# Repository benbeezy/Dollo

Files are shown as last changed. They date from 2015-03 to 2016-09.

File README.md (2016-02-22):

# Dollo
a fully printed 3D printer, that scales.

# Goals in order of priority

1) Make a 3D printer that can make as many of its own parts as possible

2) Have it so the machine can scale with little to no throwing away of old parts

3) Make it easy to assemble

4) Use no more than a single 1KG spool of plastic to make.

5) Make it as low cost as possible.

6) use parts that are easy to find.

7) make it durable (since it can print its own parts this isn't super high priority)

8) hope people stop asking "what if you could 3D print a 3D printer" because of course you can and its not that unique of an idea

# Part count and list for small Dollo

(x=number of slots times 2) -- rack_x_units.stl

13 -- extention.stl

8 -- corner.stl

156 -- bow_tie.stl but extra never hurts

96 —- long_ties.stl

2 -- x_spacer.stl

6 -- motor_mount.stl

8 -- twist_corner.stl

4 -- large_gear.stl

3 -- gear.stl

4 -- middle_gear.stl

1 -- gear_one.stl

1 -- hot_end_mount.stl

Metal parts we hope to get rid of in the future

11 -- M3x40  for the motor mounts and bed gears

5 -- M3x10  for the motor mounts and bed gears

4 -- M3x20  for the z motor

4 -- M3 lock nuts  for the bed gears

Electronics and other

1 - main controller board (we use RAMBo and also like the idea of printing the pcb and solding the components your self)

3 - end stop switches   we are trying to come up with a clever way of doing with with printed conductive parts

5 - motors

1 - hotend or whatever tool tip you want really

1 - hobbed thing, gear or bolt

1 - bearing for extruder (might be able to print)

1 - heated bed

1 - glass/aluminum that fits on the bed

4 - springs and screw for leveling your bed.

Options for a larger printer

8 - extention_3_units.stl  This will make it so your printer can fit a normal heated bed in the normal way and not limit the space at all

4 - extention_x_units & more twist_corner.stl. You can add as many of whatever size you want pieces into the z axis, this print doesn't been anything extra for those to work

# How to assemble
1) start with the basic frame, take a single corner and butt joint all 3 extension pieces to it with all 4 bow_tie slots. then on the end of each of those add corner pieces then extension pieces again until you have built out a full cube shape.

2) put on the racks. first you need to decide what side you want to be up, this really doesn't matter since it should be the same on all sides. Once you have figured that out, you can start putting your slots on the top of your printer with more bow ties add racks on parallel sides and to the top of your remaining extension piece. each should have 3 racks on it.

3) mounting your motors. first you will need to put a gear.scad on your motor shaft, then you can take a motor and put the motor_mount_small on it and screw in the single counter sunk screw on the bottom using a M3x10 and then put it on your printer rack and make sure the gear aligned with the rack teeth. once it does you can keep it on the rack and screw in your other motor_mount_small to the other side. (make sure to do this on the printer because if you don't it wont go on after) do this for all 3 racks and make sure the motor faces out.

4) mounting the x axis. grab your x_spacer and put them on the end of what you already have assembled on the left over extention piece and then slide that into the motor mount on each side of the printer.

5) Get the frame ready for the bed. first you need to prep you printer by taking the crazy looking twist_corner pieces and bow tie them to the inside of the printers frame mirroring each other but keep the bottom one out on each side.

6) now take a motor and mount put the gear_one on it and mount that to your bed, then take your middle_gear and put those next to the motor and then put your large_gear and large_twist together, and put those next in line. 

7) putting the bed in. This can be kind of tricky, but you have to twist your bed so it goes inside the frame sideways and the you should be-able to twist it to make it fit in the frame with the corners sticking out. and this is why we didn't put in the bottom corner_twists, because now your bed sits just under them and once you have the electronics set up it will be able to twist into those and once its in the teeth you will be able to add your last parts under it.

8) Electricity is fun. take all of your motor and put them into the correct stepper controllers making sure that your Y motors are plugged in opposite of each other. Plug in your electronics and make sure to upload the correct Dollo version of marlin. Once you have done this you should be able to move your motors and this is where you move your z motor in the negative direction (negative because that make the hotend and the bed closer) and once it is up at the top, you can put your last twist_corners on your printer.

9) hot ends and end stops. at the point of making this commit I do not yet have the end stops figured out. But the hotend should put in your hotend mount and should just slide and clip into your x motor mount. 

10) setting up the extruder. Not sure what extruder we are going to use yet, but if you have done 3D printing before you should know how all of that works and be able to get it going.

Z options) I do have the z axis all modeled for being fully printed and able to scale

# Extra cool facts

1) I came up with the original version of this when I was 16 and in high school and it was done in blender because thats all I knew how to use

2) This printer as it stands is under 1KG of printed parts 

3) We printed the first Dollo on 3 Prusa Mendal printer that were printer on other printers them selves and so on, all the way back to the start, so these machine have only open-source in their genealogy

4) I lived 300 miles from the printer that I used and did all of the printing over the internet using octopi to print the first Dollo

5) The Dollo can (if you want) have a metal core structure, we built it in just in case and it saved plastic so it was a win win.

6) The Dollo was made by a me and my dad, I didn't the modeling and he helped me come up with ideas on how to fix the issues I has on the way, and he test fit most of the pieces (the printers were at his house)

7) The Dollo has swappable tool heads so you can mill metal parts if you want!

8) We had no plans on how this was going to work before starting. We have gone through probably close to a 50 different ideas on how this thing should even work.

9) Half way though we almost gave up on the z and made the Dollo a Delta style printer (might still have something like that in the future)

10) We looked at a lot of other peoples printer before we could figure out how to do this one, we really could not have done it with out the community.

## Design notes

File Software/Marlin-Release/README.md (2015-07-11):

# Marlin 3D Printer Firmware


 Documentation has moved to [marlinfirmware.org](http://www.marlinfirmware.org).

## Release Branch

The Release branch contains the latest tagged version of Marlin (currently 1.0.2 – January 2015). It also includes a version 1.0.1 (December 2014). Any version of Marlin before 1.0.1 (when we started tagging versions) can be collectively referred to as Marlin 1.0.0.

For the most up-to-date Marlin code, please go to the [Development branch](https://github.com/MarlinFirmware/Marlin/tree/Development) – __Not for production use – use with caution!__ When reporting any issues, please check to see if they are resolved in the Development branch first. But let us know if issues exist in tagged releases so we may document and patch them.

## Current Status: In Development

Marlin development is being accelerated to catch up with a long list of issues. Check the Issues and Pull Requests links on the right to to see what we are currently working on.




##### [RepRap.org Wiki Page](http://reprap.org/wiki/Marlin)

## Contact

__Google Hangout:__ <a href="https://plus.google.com/hangouts/_/gxn3wrea5gdhoo223yimsiforia" target="_blank">. Hangout</a> We have a hangout every 2 weeks. Search the issue list for "Hangout" and you will see what time and date the next event is going on.

## Credits

The current Marlin dev team consists of:

 - Scott Lahteine [@thinkyhead] - English
 - Andreas Hardtung [@AnHardt] - Deutsch, English
 - [@Wurstnase] - Deutsch, English
 - [@fmalpartida] - English, Spanish
 - [@CONSULitAS] - Deutsch, English
 - [@maverikou]
 - Chris Palmer [@nophead]
 - [@paclema]
 - [@epatel]
 - Erik van der Zalm [@ErikZalm]
 - David Braam [@daid]
 - Bernhard Kubicek [@bkubicek]

More features have been added by:
  - Lampmaker,
  - Bradley Feldman,
  - and others...

## License

Marlin is published under the [GPL license](/Documentation/COPYING.md) because We believe in open development.
Do not use this code in products (3D printers, CNC etc) that are closed source or are crippled by a patent.



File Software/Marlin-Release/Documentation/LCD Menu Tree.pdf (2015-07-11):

# Marlin LCD Menu Tree

Main Menu | Tune Menu | Move Menu
Info screen | Main | Prepare
Tune | Speed | Move 10mm | Move Menu
Prepare | Nozzle | Move 1mm | Move axis
Control | Nozzle2 | Move 0.1mm | Move X
Pause print | Nozzle3 | | Move Y
Resume print | Bed | | Move Z
Stop print | Fan speed | Temperature Menu | Extruder
Print from SD | Flow | Control
Change SD card | Babystep X | Nozzle
No SD card | Babystep Y | Nozzle2
Init. SD card | Babystep Z | Nozzle3
| Change filament | Bed
| | Fan speed
| | Autotemp
| Prepare Menu | \002 Min
| Main | \002 Max | Preheat PLA
| Autostart | \002 Fact | Temperature
| Disable steppers | PID-P | Fan speed
| Auto home | PID-I | Nozzle
| Preheat PLA | PID-D | Bed
| Preheat ABS | PID-C | Store memory
| Cooldown | Preheat PLA conf
| Switch power off | Preheat ABS conf | Preheat ABS
Switch power on | Temperature
Move axis | Fan speed
| Motion Menu | Nozzle
| Control | Bed
Control Menu | Z Offset | Store memory
Main | Accel
Temperature | Vxy-jerk
Motion | Vz-jerk
LCD contrast | Ve-jerk
Retract | Vmax x
Store memory | Vmax y
Load memory | Vmax z
Restore failsafe | Vmax e
| Vmin
| VTrav min
SD Card Menu | Amax x
Main | Amax y
Refresh | Amax z
filenames | Amax e
| A-retract
| Xsteps/mm
| Ysteps/mm
| Zsteps/mm
| Esteps/mm
| Endstop abort

Retract Menu
Control
AutoRetr.
Retract mm
Retract F
Hop mm
UnRet +mm
UnRet F

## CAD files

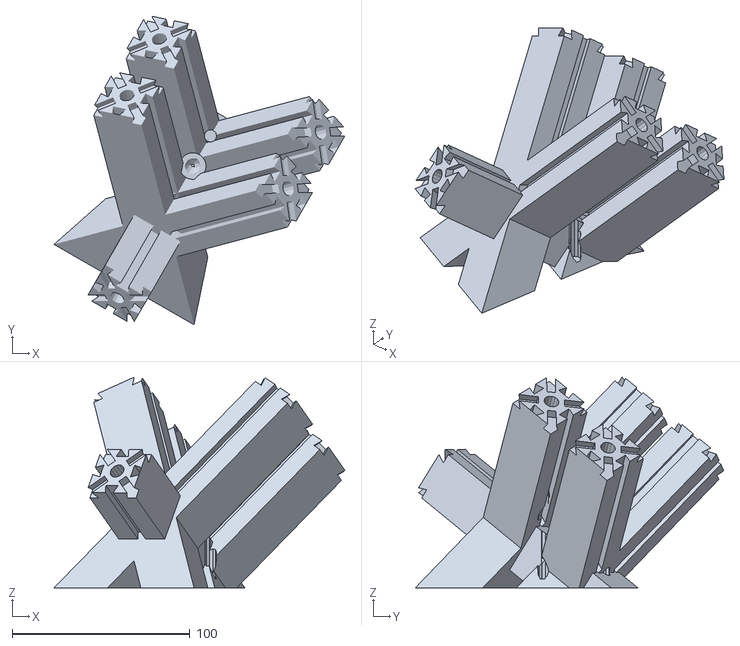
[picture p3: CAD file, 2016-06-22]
delta/corner_extra.stl
163.9 x 173.8 x 118.7

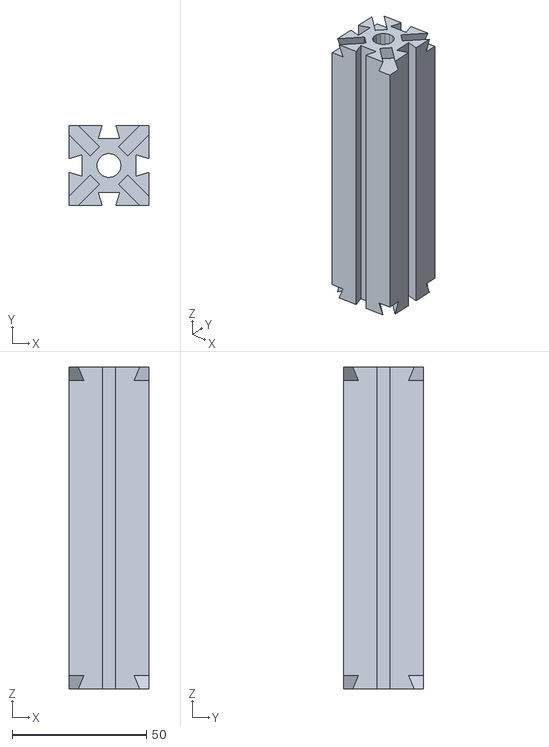
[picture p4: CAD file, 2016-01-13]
mockup/blender_model/extention.stl
30.0 x 30.0 x 120.0

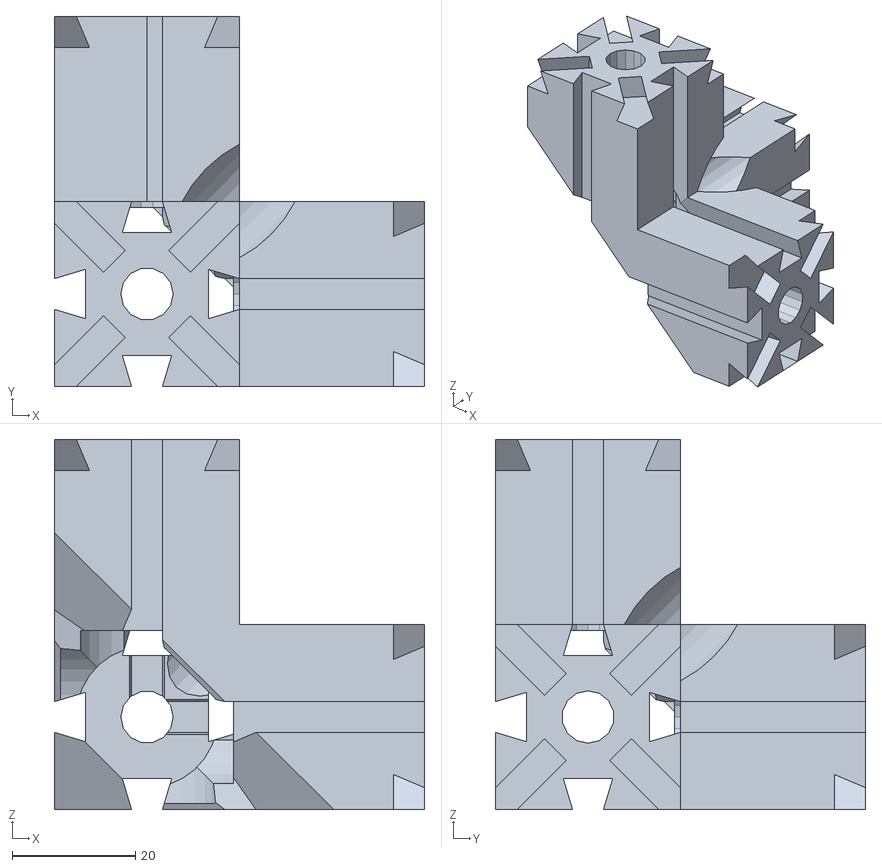
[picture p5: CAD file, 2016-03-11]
NEW_long_ties/blender_mockup/corner.stl
60.0 x 60.0 x 60.0

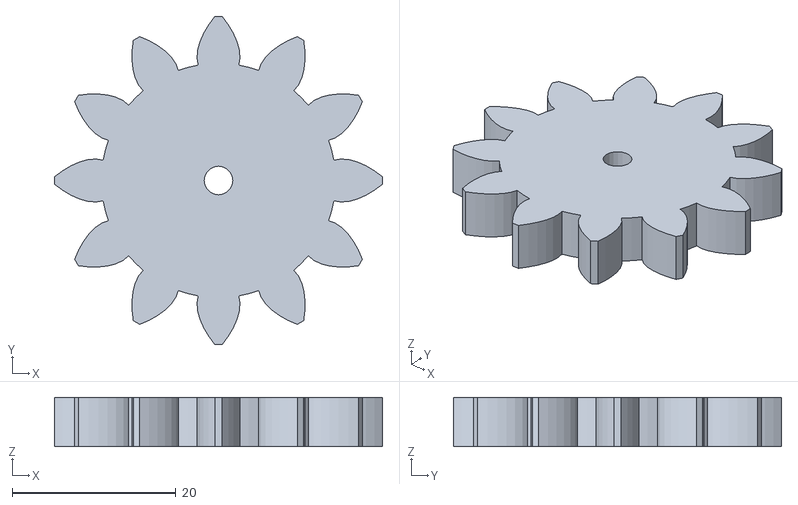
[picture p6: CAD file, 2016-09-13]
NEW_long_ties/STL/gear_middle.stl
40.1 x 40.1 x 6.00

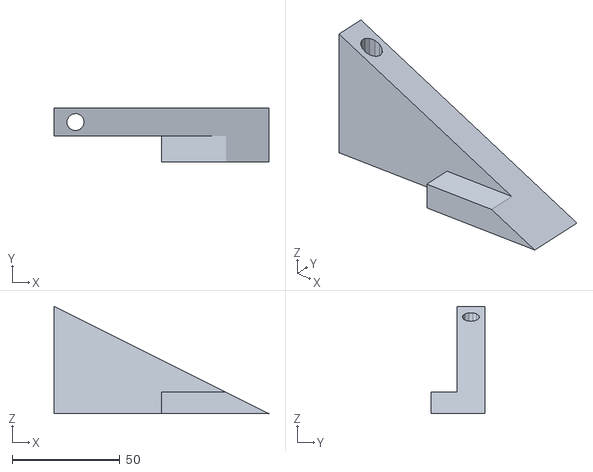
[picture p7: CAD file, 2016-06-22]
NEW_long_ties/temp_z_metal.stl
100.0 x 25.0 x 50.0

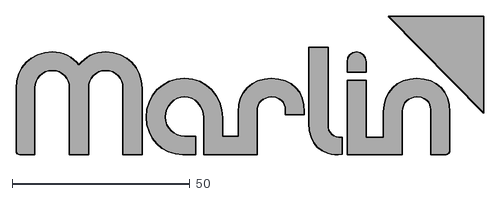
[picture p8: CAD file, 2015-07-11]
Software/Marlin-Release/Documentation/Logo/Marlin Logo.dxf
131.6 x 39.5

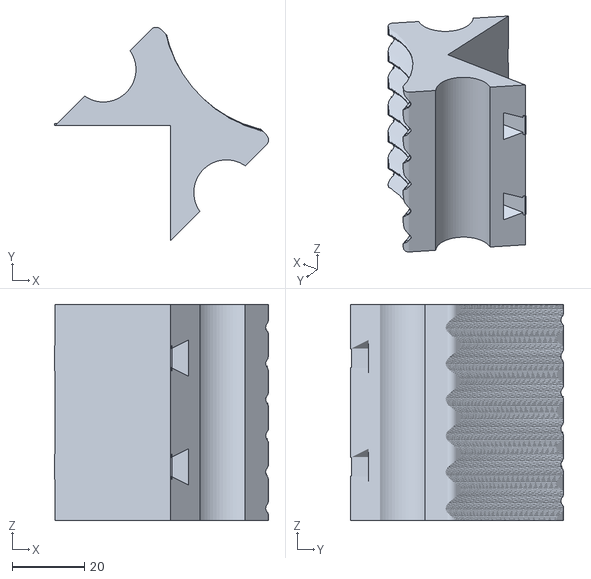
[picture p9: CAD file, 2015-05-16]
stl/twist_corner.stl
59.1 x 58.9 x 59.8

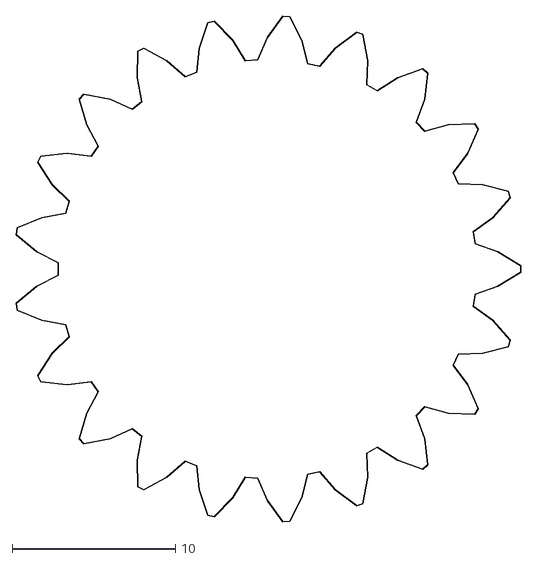
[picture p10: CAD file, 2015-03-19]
vectors/gear.dxf
30.8 x 30.9

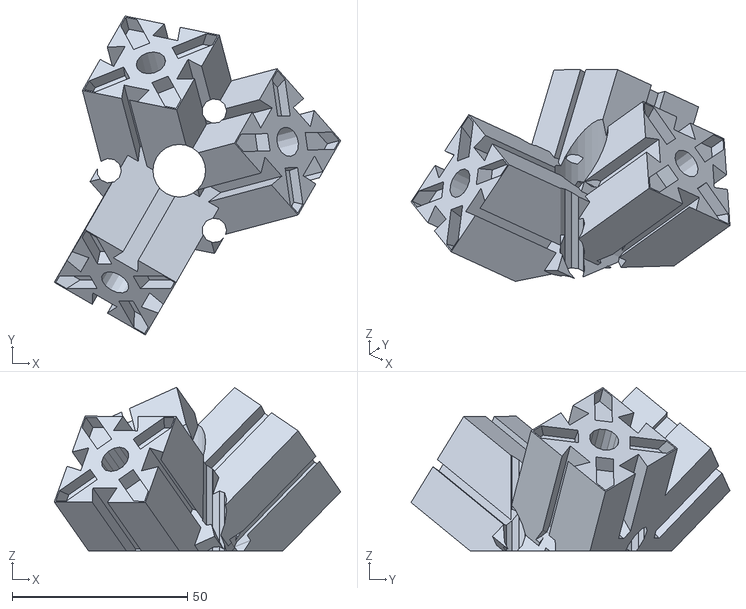
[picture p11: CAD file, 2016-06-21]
delta/corner.stl
81.7 x 90.9 x 46.6

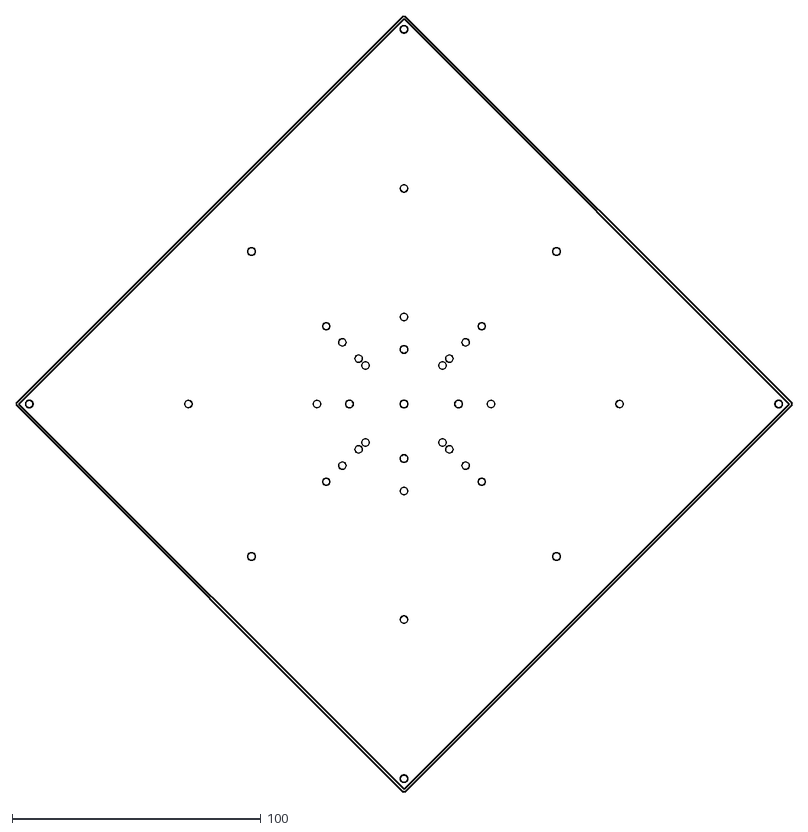
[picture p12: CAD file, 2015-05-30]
NEW_long_ties/mockup.dxf
311.8 x 311.8

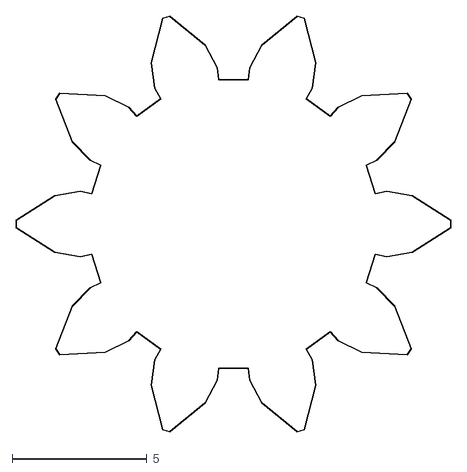
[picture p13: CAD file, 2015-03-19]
NEW_long_ties/small_gear.dxf
16.2 x 15.5

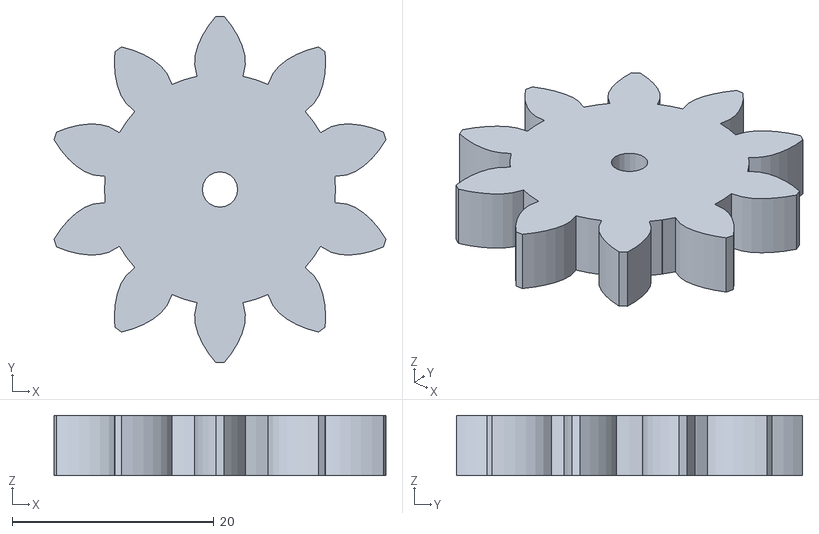
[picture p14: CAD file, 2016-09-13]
NEW_long_ties/STL/gear_rev_gear_two.stl
32.9 x 34.4 x 6.00

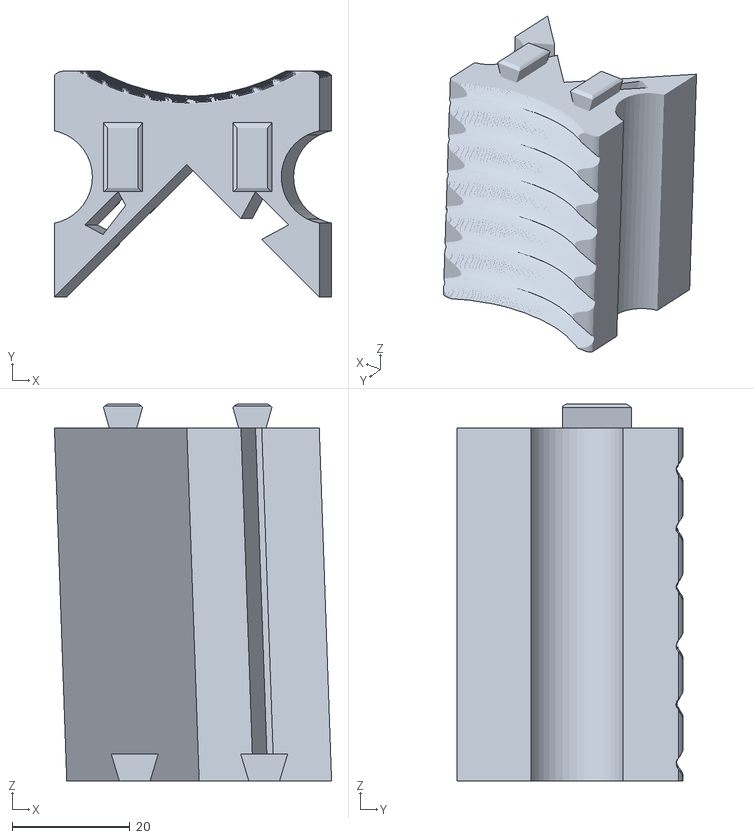
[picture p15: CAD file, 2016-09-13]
NEW_long_ties/STL/twist_corner.stl
47.1 x 38.4 x 64.1

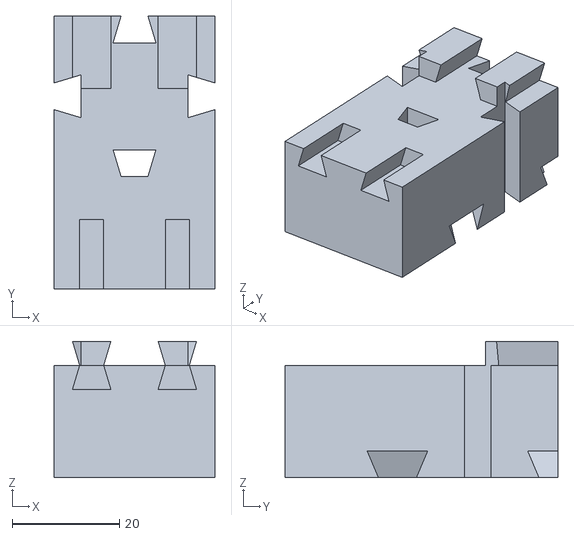
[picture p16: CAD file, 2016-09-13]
NEW_long_ties/STL/x_spacer.stl
30.0 x 51.0 x 25.5

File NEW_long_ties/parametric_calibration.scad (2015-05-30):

/*
what do you want to test for?

In the section below, set what you want to test to true, 
and things that you dont want to test to false.

logo will test sharp corners and thin objects
x_axis will test your x length and your resolution on text
y_axis will test rounded faces in all directions and your y axis length
z_axis will test your z height with 5mm units, small overhangs, and how will it does small surfaces

*/

//what do you want to test?

x_axis = true;
y_axis = true;
z_axis = true;
overhangs = true;
sharp_corners = true;
thin_objects = true;

//how big in mm do you want your test to be?

x = 50;
y = 50;
z = 50;











// dont mess with these things unless you know what you are doing
module logo(){
	difference(){
		translate([5,5,0]) cube([20,20,3]);
		translate([12,10,-.5]) cube([8,50,4]);
		translate([12,0,-.5]) cube([1,50,4]);
		translate([12,25,-.5]) rotate([0,0,-70]) cube([8,50,4]);
		translate([12,5,-.5]) rotate([0,0,-70]) cube([8,50,4]);
		translate([-15,28,-.5]) rotate([0,0,-80]) cube([8,50,4]);
		translate([12,-3,-.5]) rotate([0,0,70]) cube([8,50,4]);
	}
	translate([5,5,0]) cube([20,20,.5]);
}


module x(){
	difference(){
		cube([x,5,3]);
		for ( i = [0 : x/5-1] )
			{	
				translate([(i*5)+1,0,2.8]) cube([.25,3,.5]);
			}
	}
	linear_extrude(height=3.){
		translate([5,3.5,2.8]) text("5", size = 1.5);
		translate([5*2,3.5,2.8]) text("10", size = 1.5);
		translate([5*3,3.5,2.8]) text("15", size = 1.5);
		translate([5*4,3.5,2.8]) text("20", size = 1.5);
		translate([5*5,3.5,2.8]) text("25", size = 1.5);
		translate([5*6,3.5,2.8]) text("30", size = 1.5);
		translate([5*7,3.5,2.8]) text("35", size = 1.5);
		translate([5*8,3.5,2.8]) text("40", size = 1.5);
		translate([5*9,3.5,2.8]) text("45", size = 1.5);
	}
}

module y(){
	hull(){
		translate([2.5,0,5/2]) sphere(d=5, $fn=80);
		translate([2.5,50,0]) cylinder(h=3, d=5, $fn=80);
	}
}

module z(){
	intersection(){
		cube([10,10,50]);
		hull(){
			sphere(d=12, $fn=80);
			translate([0,0,50]) sphere(d=8, $fn=80);
		}
	}
}

 if (x_axis==true || overhangs==true) {
	  if (overhangs==true) {
			difference(){
				x();
				translate([5,0,0]) cube([5,3,2]);
				translate([15,0,0]) cube([10,3,2]);
				translate([30,0,0]) cube([15,3,2]);
			}
		} else{
			x();
		}
 }
 
  if (y_axis==true) {
	difference(){
		y();
		for ( i = [0 : x/5-1] )
			{	
				translate([0,(i*5)+1,0]) cube([3,.25,.5]);
			}
	}
 }
 
  if (z_axis==true) {
		z();
		for ( i = [0 : x/5-1] )
			{	
				translate([0,-.25,(i*5)+1]) cube([4,1,.25]);
			}
 }

  if (thin_objects==true || sharp_corners==true) {
		logo();
 }

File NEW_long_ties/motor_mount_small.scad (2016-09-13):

///////// NEED TO REDO THE MATH BECUASE OF THE SNAP ON RAILS, WELL WORTH IT

$fn = 30;
include <globals.scad>;
include <include.scad>;


frame_width = 35.5;
tail_depth = 11;
mount_max = 62.5;
wabble = 1.5;
not_tooth_gap = 0;
rack_gap = 2.5;
tower_height = 17.5+3;

text = "Dollo";
font = "Liberation Sans";

hole_length = 0.8;

//$fn=220;

diameter = 3.5;

module rounded_cube(width,depth,height){
    hull(){
        translate([width/2-diameter/2,depth/2-diameter/2,height/2-diameter/2]) sphere(d=diameter);
        translate([width/2-(diameter/2),depth/2-(diameter/2),-height/2+(diameter/2)]) sphere(d=diameter);
        translate([-width/2+diameter/2,depth/2-diameter/2,height/2-diameter/2]) sphere(d=diameter);
        translate([-width/2+(diameter/2),depth/2-(diameter/2),-height/2+(diameter/2)]) sphere(d=diameter);
        
        translate([width/2-diameter/2,-depth/2+diameter/2,height/2-diameter/2]) sphere(d=diameter);
        translate([width/2-(diameter/2),-depth/2+(diameter/2),-height/2+(diameter/2)]) sphere(d=diameter);
        translate([-width/2+diameter/2,-depth/2+diameter/2,height/2-diameter/2]) sphere(d=diameter);
        translate([-width/2+(diameter/2),-depth/2+(diameter/2),-height/2+(diameter/2)]) sphere(d=diameter);
    }
}    
//rounded_cube(x,y,z,diameter);


module y_mount_added(){    
    
    translate([0,2.25-2.25+rack_gap/2,-1]) rounded_cube(depth = 50+rack_gap*2, width = frame_width+15+1, height=4, center=true);
    
	translate([0,frame_width-15.5+rack_gap,2.5]) rounded_cube(height = 5, width = 50, depth = 11, diameter = 3.5);
//towers
    echo ((17.5+4.25)/2);
	translate([0-21,-25.75,0.625]) cube([42,18,tower_height]);
	translate([(32-21-4)+18/2,(11-21+wabble)+15/2,(17.5+4.25)/2]) rounded_cube(18,15,tower_height);
	translate([(-21-4)+25/2,    (11-21+wabble)+15/2,(17.5+4.25)/2]) rounded_cube(25,15,tower_height);

	//#translate([17,(not_tooth_gap/2)+5,2.5]) rounded_cube(height = 4, width = 15, depth = not_tooth_gap, diameter = 2);
	//#translate([-17,(not_tooth_gap/2)+5,2.5]) rounded_cube(height = 4, width = 15, depth = not_tooth_gap, diameter = 2);
}

module bolt_hole() {
    hull() {
        cylinder(d=3.5, h=70);
        translate([hole_length,hole_length,0]) cylinder(d=3.5, h=70);
    }
}

module bolt_head_hole() {
    hull() {
        cylinder(d=6, h=3);
        translate([hole_length,hole_length,0]) cylinder(d=6, h=3);
    }
}

module y_mount_taken(){
	halign = [
	   [0, "center"]
	 ];
	 
		 rotate([0,0,-90]) for (a = halign) {
		   translate([-15, 15,-3]) {
			 linear_extrude(height = 1) {
			   text(text = str(text), font = font, size = 8, halign = a[1]);
			 }
		   }
		 }
		 rotate([0,0,90]) for (a = halign) {
		   translate([15,15,-3]) {
			 linear_extrude(height = 1) {
			   text(text = str(text), font = font, size = 8, halign = a[1]);
			 }
		   }
		 }
		 
	rotate([0,0,45]) {
        translate([5.65-21,5.65-21,-10]) bolt_hole();
		translate([5.65+31-21,5.65-21,-10]) bolt_hole();
		translate([5.65-21,5.65+31-21,-10]) bolt_hole();
		translate([5.65+31-21,5.65+31-21,-10]) bolt_hole();

		//counter sink

        #translate([5.65-21,5.65-21,-3]) bolt_head_hole();
		#translate([5.65+31-21,5.65-21,-3]) bolt_head_hole();
		#translate([5.65-21,5.65+31-21,-3]) bolt_head_hole();
		#translate([5.65+31-21,5.65+31-21,2.5]) bolt_head_hole();

		translate([-70,-30,-5]) cube([50,50,50]);
		translate([-30,-70,-5]) cube([50,50,50]);

		translate([0,0,-5]) cylinder(d=23, h=20);
        translate([hole_length,hole_length,-5]) cylinder(d=23, h=20);

		#rotate([90,0,-45]) translate([-8,-3,-55+tail_depth]) male_dovetail(height=30);
		#rotate([90,0,-45]) translate([8,-3,-55+tail_depth]) male_dovetail(height=30);

		#rotate([90,0,-45]) translate([-8,-3,22-tail_depth]) male_dovetail(height=30);
		#rotate([90,0,-45]) translate([8,-3,22-tail_depth]) male_dovetail(height=30);
	}
}

module motor_mount(){
	difference(){
		y_mount_added();
		y_mount_taken();
	}
}

module translated_mount(){
translate([(-obj_leg/2)-2.5,0,0]) rotate([0,90,0]) motor_mount();
}

module screw_driver(){
translated_mount();
}

rotate([0,-90,0]) difference(){
	screw_driver();
	translate([-15,0,0]) rotate([0,90,0]) union(){
		translate([5.65,5.65,-1]) cylinder(d=3.5, h=40);
		translate([5.65+31,5.65,-1]) cylinder(d=3.5, h=40);
		translate([5.65,5.65+31,-1]) cylinder(d=9, h=40);
		translate([5.65+31,5.65+31,-1]) cylinder(d=9, h=40);

		translate([-20,20,15]) rotate([90,0,45]) cylinder(h=70, d=22);
		translate([20,20,15]) rotate([90,0,-45]) cylinder(h=70, d=22);
	}
}

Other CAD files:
mockup/blender_model/corner.stl
NEW_long_ties/blender_mockup/extention.stl
NEW_long_ties/STL/gear_one.stl
NEW_long_ties/STL/long_bow_tie_unaligned.stl
mockup/blender_model/motor_mount_small.scad
NEW_long_ties/STL/Old_extention_v2.stl
NEW_long_ties/STL/aitrippers_bowden_mount.stl
NEW_long_ties/STL/bed_carriage.stl
NEW_long_ties/STL/bow_tie.stl
NEW_long_ties/STL/corner.stl
NEW_long_ties/STL/endstop.stl
NEW_long_ties/STL/extention.stl
NEW_long_ties/STL/extention_metal_z.stl
NEW_long_ties/STL/extention_side.stl
NEW_long_ties/STL/gear.stl
NEW_long_ties/STL/gear_middle_scaled.stl
NEW_long_ties/STL/gear_rev_gear_one.stl
NEW_long_ties/STL/hot_end_mount.stl
NEW_long_ties/STL/long_bow_tie.stl
NEW_long_ties/STL/long_bow_tie_half.stl
NEW_long_ties/STL/long_tie.stl
NEW_long_ties/STL/motor_mount_small.stl
NEW_long_ties/STL/rack.stl
NEW_long_ties/STL/rack_8.stl
NEW_long_ties/STL/z_endstop_holder.stl
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

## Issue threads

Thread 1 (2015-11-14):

Make my own

Fafadu40, 2015-11-14:
Hi !
I'm interested in your project and  would like to print a working 3D printer with your repo.
However, I'm a bit lost with all that, what are the best slicing parameters and pieces I've gotta print and how big is the biggest piece (to know if I can print it on my friend's printer).
I already read your instructable.

Thanks for answering.

wildseyed, 2015-11-14:
@Fafadu: The largest pieces are actually made from smaller pieces that snap together.  Even a very small 3D printer will be able to print this.

Fafadu40, 2015-11-14:
And what about the density or slicing ? What are the best infill and layers ?

benbeezy, 2015-11-16:
@Fafadu40 for the infill I use something around 20-25% and 2 solid layers on top bottom and 2 parameters. I think I even have a slicer config file in the git repo (not sure how up to date it is so you should check first)

Fafadu40, 2015-11-16:
So if I print a basic size, how much plastic do I need ?

benbeezy, 2015-11-16:
You should be able to print everything with a one kg spool, it will use up
the entire spool though.

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

Fafadu40, 2015-11-16:
OK thanks. It's a student project so I think I'll be back there to ask some more questions :)

benbeezy, 2015-11-16:
Feel free to ask anything you want :) im willing to answer anything. I
would say try to print the long ties directory. It looks better and is
stronger in the joints.
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

Fafadu40, 2015-11-16:
What's different with those long ties ?

benbeezy, 2015-11-16:
If you look at the stl files I rotated the slots to go with the length
instead of across it. So it uses sliding joints now. So you can have 8
contact points where pieces join instead of just 4 I printed one out and it
is going to be the version 2 of the dollo.
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

Closed 2016-02-07.

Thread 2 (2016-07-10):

Printable Bed Mount/Carriage

sarf2k4, 2016-07-10:
Hi, is there any considerations to have a printable bed mount/carriage instead of drilling a hole in the acrylic?

Here is my fully printable y carriage meant to be used on prusa based structure. I believe these can be incorporated here as well

v2 - http://www.thingiverse.com/thing:1319196
v3 - http://www.thingiverse.com/thing:1345816

spegelius, 2016-07-27:
I did some openscadding and designed a modular bed carriage, commit here: https://github.com/spegelius/Dollo/commit/90b00451724bb7ac4423c7c2c93818054710ddfc.
I did print the center piece and arm, seems to fit together. Need to print the rest to see how well the dimensions match the gears and bed itself.

benbeezy, 2016-09-13:
These files are now merged into master so I am going to close this issue. If you have any other issues with missing models or maybe if something doesn't quite print right please feel free to open another issue

Closed 2016-09-13.

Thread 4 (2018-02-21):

Is the project alive?

szerwi, 2018-02-21:
Hi,

Is this project sill alive? Is the project completed so I can print it and it will work? Is there any documentation with some instructions and list with parts I need to print (I know it is wrote on Github, but maybe it is wrote somewhere else)?

mlaga97, 2018-02-26:
I don't think this particular repository is active anymore.

This printer is more of an experiment in the philosophy of RepRap then something that should be built with the intent of being able to print anything other than test prints. I did a lot of refactoring and made a lot of changes in my fork over the course of about 3 months, and I managed to get a pretty cool toy that does occasionally spit out plastic in vaguely recognizable forms, but it is certainly a long ways away from being able to print out its own parts. One of the other forks may have gotten farther than I did.

If you want to build one (which will require a lot of tweaking and OpenSCAD skills to make improvements), I would suggest looking at some of the forks:
* [mlaga97/Dollo](https://github.com/mlaga97/Dollo)
* [spegelius/Dollo](https://github.com/spegelius/Dollo)
* [Virindi-AC/Whitney](https://github.com/Virindi-AC/Whitney)

Alternatively, if you want a more mature and more actively developed project with a similar philosophy, I would highly suggest looking into the Hangprinter project.

spegelius, 2018-02-26:
Yeah, I think I'm the only one working with the original Dollo. Well it has evolved somewhat so a Dollo MK2 or something...
I get relatively good prints out of my Dollo build and use it quite a lot for prints that don't need to be pristine, but still dimensionally accurate. Granted, I'm using metal rods for Z at the moment. Z-axis is the biggest problem of the original design. Im working on some ideas for making it printable with good quality, though.
Also building another Dollo currently, I'm posting info about that here: http://3dprintboard.com/showthread.php?12856-Dollo-3D-Printable-3D-Printer (check tha last pages for up to date info)

spegelius, 2018-02-26:
You can print it and it might even work somewhat. But it will need tinkering...

szerwi, 2018-02-26:
Will the print quality be good? Or I need upgrades like metal Z rod?

spegelius, 2018-02-26:
Well it seems that the latest commits that were merged from my branch were still about the large gears for z-axis, which causes bad quality: https://www.dropbox.com/s/oowlddhd8ystile/2016-09-06%2012.25.30.jpg?dl=0. That vase should have straight lines and surfaces... the gears just cause the bed to twist around when they turn.
The metal z parts that I designed aren't merged here.

szerwi, 2018-02-26:
So I should print gear.stl, not gear_large.stl?

spegelius, 2018-02-26:
Please don't print anything you don't understand, The status in this repository is very much work in progress. I haven't looked at those parts for more than a year and can only remember that it was a PITA to get working. And there are more than one gear to print to get the whole z-axis contraption to work... I don't even remember if I saved the correct sized gears so you'll be printing stuff pretty much blind.

szerwi, 2018-02-26:
:/ So I think I won't be able to print Dollo. I don't know how to use OpenSCAD.

spegelius, 2018-02-26:
Not this version, there's no instructions for all parts and some of the parts are most definitely EOL. If you want to build a working Dollo, follow the build I'm doing and hopefully in the end I've explained everything well enough for others to get a working printer-like thing assembled.

szerwi, 2018-02-26:
Do you know when you will finish the build? And the Dollo that you are building will be fully printable, or it will have some mods like metal Z rods?

spegelius, 2018-02-26:
Month or two, depending how much time I can use on it. I'm planning on mostly printable, yes. Metal z rods are an option if things don't work out well enough with the printable z.

szerwi, 2018-02-26:
Ok, so I'm waiting for your finish and instructions :)

szerwi, 2018-02-26:
@spegelius Are you sure that you will make instructions how to build Dollo when you finish? :) If yes, I will order electronics from China now and start printing Dollo when you will make instructions :)

spegelius, 2018-02-27:
Well I've already built 1/3 of the new one and also written it down in the forum posts so I very much intend to finish :)

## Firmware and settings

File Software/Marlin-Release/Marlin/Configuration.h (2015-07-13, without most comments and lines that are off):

#define CONFIGURATION_H
#include "boards.h"
#define STRING_VERSION_CONFIG_H __DATE__ " " __TIME__ // build date and time
#define STRING_CONFIG_H_AUTHOR "(none, default config)" // Who made the changes.
#define SERIAL_PORT 0
#define BAUDRATE 115200
  #define MOTHERBOARD 33
#define EXTRUDERS 1
#define POWER_SUPPLY 1
#define TEMP_SENSOR_0 1
#define TEMP_SENSOR_1 1
#define TEMP_SENSOR_2 0
#define TEMP_SENSOR_BED 0
#define MAX_REDUNDANT_TEMP_SENSOR_DIFF 10
#define TEMP_RESIDENCY_TIME 10  // (seconds)
#define TEMP_HYSTERESIS 3       // (degC) range of +/- temperatures considered "close" to the target one
#define TEMP_WINDOW     1       // (degC) Window around target to start the residency timer x degC early.
#define HEATER_0_MINTEMP 5
#define HEATER_1_MINTEMP 5
#define HEATER_2_MINTEMP 5
#define BED_MINTEMP 5
#define HEATER_0_MAXTEMP 275
#define HEATER_1_MAXTEMP 275
#define HEATER_2_MAXTEMP 275
#define BED_MAXTEMP 150
#define PIDTEMP
#define BANG_MAX 255 // limits current to nozzle while in bang-bang mode; 255=full current
#define PID_MAX BANG_MAX // limits current to nozzle while PID is active (see PID_FUNCTIONAL_RANGE below); 255=full current
  #define PID_FUNCTIONAL_RANGE 10 // If the temperature difference between the target temperature and the actual temperature
  #define PID_INTEGRAL_DRIVE_MAX PID_MAX  //limit for the integral term
  #define K1 0.95 //smoothing factor within the PID
  #define PID_dT ((OVERSAMPLENR * 10.0)/(F_CPU / 64.0 / 256.0)) //sampling period of the temperature routine
    #define  DEFAULT_Kp 22.2
    #define  DEFAULT_Ki 1.08
    #define  DEFAULT_Kd 114
#define MAX_BED_POWER 255 // limits duty cycle to bed; 255=full current
#define PREVENT_DANGEROUS_EXTRUDE
#define PREVENT_LENGTHY_EXTRUDE
#define EXTRUDE_MINTEMP 170
#define EXTRUDE_MAXLENGTH (X_MAX_LENGTH+Y_MAX_LENGTH) //prevent extrusion of very large distances.
#define ENDSTOPPULLUPS // Comment this out (using // at the start of the line) to disable the endstop pullup resistors
  #define ENDSTOPPULLUP_XMAX
  #define ENDSTOPPULLUP_YMAX
  #define ENDSTOPPULLUP_ZMAX
  #define ENDSTOPPULLUP_XMIN
  #define ENDSTOPPULLUP_YMIN
  #define ENDSTOPPULLUP_ZMIN
const bool X_MIN_ENDSTOP_INVERTING = true; // set to true to invert the logic of the endstop.
const bool Y_MIN_ENDSTOP_INVERTING = true; // set to true to invert the logic of the endstop.
const bool Z_MIN_ENDSTOP_INVERTING = true; // set to true to invert the logic of the endstop.
const bool X_MAX_ENDSTOP_INVERTING = true; // set to true to invert the logic of the endstop.
const bool Y_MAX_ENDSTOP_INVERTING = true; // set to true to invert the logic of the endstop.
const bool Z_MAX_ENDSTOP_INVERTING = true; // set to true to invert the logic of the endstop.
#if defined(COREXY) && !defined(DISABLE_MAX_ENDSTOPS)
  #define DISABLE_MAX_ENDSTOPS
#endif
#define X_ENABLE_ON 0
#define Y_ENABLE_ON 0
#define Z_ENABLE_ON 0
#define E_ENABLE_ON 0 // For all extruders
#define DISABLE_X false
#define DISABLE_Y false
#define DISABLE_Z false
#define DISABLE_E false // For all extruders
#define DISABLE_INACTIVE_EXTRUDER true //disable only inactive extruders and keep active extruder enabled
#define INVERT_X_DIR true    // for Mendel set to false, for Orca set to true
#define INVERT_Y_DIR false    // for Mendel set to true, for Orca set to false
#define INVERT_Z_DIR true     // for Mendel set to false, for Orca set to true
#define INVERT_E0_DIR false   // for direct drive extruder v9 set to true, for geared extruder set to false
#define INVERT_E1_DIR false    // for direct drive extruder v9 set to true, for geared extruder set to false
#define INVERT_E2_DIR false   // for direct drive extruder v9 set to true, for geared extruder set to false
#define X_HOME_DIR -1
#define Y_HOME_DIR -1
#define Z_HOME_DIR -1
#define min_software_endstops true // If true, axis won't move to coordinates less than HOME_POS.
#define max_software_endstops true  // If true, axis won't move to coordinates greater than the defined lengths below.
#define X_MAX_POS 205
#define X_MIN_POS 0
#define Y_MAX_POS 205
#define Y_MIN_POS 0
#define Z_MAX_POS 200
#define Z_MIN_POS 0
#define X_MAX_LENGTH (X_MAX_POS - X_MIN_POS)
#define Y_MAX_LENGTH (Y_MAX_POS - Y_MIN_POS)
#define Z_MAX_LENGTH (Z_MAX_POS - Z_MIN_POS)
#define Z_PROBE_REPEATABILITY_TEST  // If not commented out, Z-Probe Repeatability test will be included if Auto Bed Leveling is Enabled.
#define MANUAL_X_HOME_POS 0
#define MANUAL_Y_HOME_POS 0
#define MANUAL_Z_HOME_POS 0
#define NUM_AXIS 4 // The axis order in all axis related arrays is X, Y, Z, E
#define HOMING_FEEDRATE {50*60, 50*60, 100, 0}  // set the homing speeds (mm/min)
#define DEFAULT_AXIS_STEPS_PER_UNIT   {78.7402,78.7402,200.0*8/3,760*1.1}  // default steps per unit for Ultimaker
#define DEFAULT_AXIS_STEPS_PER_UNIT   {63, 63, (74.3333*5)*1.5, 150}  // default steps per unit for Dollo
#define DEFAULT_MAX_FEEDRATE          {500, 500, 5, 25}    // (mm/sec)
#define DEFAULT_MAX_ACCELERATION      {9000,9000,100,10000}    // X, Y, Z, E maximum start speed for accelerated moves. E default values are good for Skeinforge 40+, for older versions raise them a lot.
#define DEFAULT_ACCELERATION          3000    // X, Y, Z and E max acceleration in mm/s^2 for printing moves
#define DEFAULT_RETRACT_ACCELERATION  3000   // X, Y, Z and E max acceleration in mm/s^2 for retracts
#define DEFAULT_XYJERK                20.0    // (mm/sec)
#define DEFAULT_ZJERK                 0.4     // (mm/sec)
#define DEFAULT_EJERK                 5.0    // (mm/sec)
#define CUSTOM_M_CODES
  #define CUSTOM_M_CODE_SET_Z_PROBE_OFFSET 851
  #define Z_PROBE_OFFSET_RANGE_MIN -15
  #define Z_PROBE_OFFSET_RANGE_MAX -5
#define PLA_PREHEAT_HOTEND_TEMP 180
#define PLA_PREHEAT_HPB_TEMP 70
#define PLA_PREHEAT_FAN_SPEED 255   // Insert Value between 0 and 255
#define ABS_PREHEAT_HOTEND_TEMP 240
#define ABS_PREHEAT_HPB_TEMP 100
#define ABS_PREHEAT_FAN_SPEED 255   // Insert Value between 0 and 255
#define SOFT_PWM_SCALE 0
#define FILAMENT_SENSOR_EXTRUDER_NUM	0  //The number of the extruder that has the filament sensor (0,1,2)
#define MEASUREMENT_DELAY_CM			14  //measurement delay in cm.  This is the distance from filament sensor to middle of barrel
#define DEFAULT_NOMINAL_FILAMENT_DIA  3.0  //Enter the diameter (in mm) of the filament generally used (3.0 mm or 1.75 mm) - this is then used in the slicer software.  Used for sensor reading validation
#define MEASURED_UPPER_LIMIT          3.30  //upper limit factor used for sensor reading validation in mm
#define MEASURED_LOWER_LIMIT          1.90  //lower limit factor for sensor reading validation in mm
#define MAX_MEASUREMENT_DELAY			20  //delay buffer size in bytes (1 byte = 1cm)- limits maximum measurement delay allowable (must be larger than MEASUREMENT_DELAY_CM  and lower number saves RAM)
#define DEFAULT_MEASURED_FILAMENT_DIA  DEFAULT_NOMINAL_FILAMENT_DIA  //set measured to nominal initially
#include "Configuration_adv.h"
#include "thermistortables.h"

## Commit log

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2015-03-21 Mock up finished, can now render the xdf to print for bed screw holes.
    TO-DO:
    format the code so that it is user friendly to see how things work and use if statments for rendering some thing and not others
    [bow_tie.scad, gears.scad, mockup.scad]
2015-03-22 mall fixes on extention and other parts as of 7:27 march 21 2015
    [extention.scad, gears.scad, hot_end_mount.scad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]
2015-03-22 the corner now has stoppers just like the extention pieces, and we arent doing scale on the slots but the bow_tie, just to keep things a little bit more consistant
    [corner.scad, extention.scad, include.scad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]
2015-03-22 dding the dxf file for the bed layout, this layout works perfect and needs no changes unless we change the gearing ont he bottom of the bed
    [mockup.dxf]
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2015-04-07 going back to xdf models for the time being, I dont yet have time to mess with the gear library and make it match what we already have.
    that will be the plan in the future though.
    [bow_tie.scad, corner.scad, extention.scad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]
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2015-04-11 Fixed the corner spacing and started adding STL files for people who just want to print it and not deal with scad files
    [corner.scad, gears.scad, twist_corner.scad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]
2015-04-12 I fixed the extention piece so that the units work better and move all aspects.
    [extention.scad, extention_3_units.stl, rack.stl]
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2015-04-13 I guess things are working better with the rack piece and I simplified a few of the other models. they work and look the same but with less stupid things in them, now it is a basic shape.
    [bow_tie.scad, corner.scad, rack.scad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]
2015-04-14 added the newest config for our slicer settings, and a few STL files. This commit is so that older ben can test the motor mounts while im on the road.
    [back_testing.stl, bow_tie.stl, front_testing.stl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]
2015-04-14 wider tooth side spacers fixed misspelling of diamiter to diameter
    [motor_mount_small.scad]
2015-04-14 motor_mount_small fixed to prevent wabble.
    [motor_mount_small.scad, motor_mount_small.stl]
2015-04-14 added firmware to the git repo. a modified Marlin for RAMBo and only RAMOo at this point in time, made it so the y is the axis that uses the double headers on the board.
    [Configuration.h, Configuration_adv.h]
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2015-04-20 changed the support on the corner to see if it will work better this way.
    [corner.scad, corner.stl]
2015-05-06 a few file updates, mostly the z works now.
    [gears.scad, twist_corner.scad, twist_corner.stl]
2015-05-10 Update now that the z is working and the endstops are in place. and the hotend-mount is better and racks are thicker and motor mount compinsated for thicker racks
    [bow_tie.scad, bow_tie.stl, endstop.scad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]
2015-05-16 I think I got the z moving witht he right math to it
    [Configuration.h]
2015-05-18 firmware changed and small mods to the spiral corners to make the layers go wtih the twist (they now print tilted at 4 deg)
    [Configuration.h, gears.scad, twist_corner.scad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]
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2015-05-30 updated the bow ties to not have flair on a printer that is to low on the first layer and we are still fine tuning the z axis with these changes
    [bed_layout.scad, bow_tie.scad, bow_tie.stl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]
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2015-06-10 trying to get the rack to fit flush with the extention pieces
    [back_testing.stl, bow_tie.scad, corner.stl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]
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2015-06-21 hotend mount is thicker and added a crew hole, so that we can try and stop the hotend from moving around while printing
    [hot_end_mount.scad]
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2015-07-11 updated the firmware and now the dollo is half working with ramps and fully working with rambo
    [Configuration.h, Configuration_adv.h, Marlin Logo.dxf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]
2015-07-13 getting rid of the old firmware and putting in the new, in the new one both ramps and ramo are working with the swapped stepper controllers
    [Configuration.h, Configuration_adv.h]
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2015-09-27 make it so everyone just needs to stl files and have no need to render out their own from the .scad files.
    the extentions stl files now have the support, and I added the 3 unit part for larger printer.
    one of the gears was not rendered out at all! But now it is and its a stl in the stl directory.
    [extention.stl, extention_3_units.stl, gear_one.stl]
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2015-09-30 the x spacer now has a spot incase your motor mounts wont counter skin the heads of the screws
    [x_spacer.scad]
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2015-11-03 STLs on the long ties, and I changed the angle of the bow tie so things will not work with the old version
    [bow_tie.stl, corner.scad, corner.stl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]
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2015-11-06 more long tie things, looks like the joints are holding up pretty good
    [bow_tie.scad, bow_tie.stl, corner.scad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]
2016-02-22 update to make things easier to tell people about
    [Configuration.h, Configuration_adv.h, Marlin Logo.dxf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]
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2016-05-24 Fixes:
    - smaller side cylinders -> more rigid parts
    - move vertical dovetail hollows wider to
    fit extention parts
    - rise top dovetail parts so next part hollows
    match
    [twist_corner.scad]
2016-05-24 Minor gear fixes
    [gears.scad, small_gear.dxf]
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2016-05-24 Move lower rectangle away a bit so rail fits
    [motor_mount_small.scad]
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2016-05-24 Style fixes, logo shows
    [logo.scad, long_bow_tie.scad]
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2016-07-17 Shorten gear and shaft's flat part, add bolt hole
    [gear.scad]
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2016-07-25 Move gear bolt hole down
    - so it's in the middle of gear groove
    [gear.scad]
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2016-07-27 Xspacer: fix bow tie hole
    [x_spacer.scad, x_spacer.stl]
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2016-07-27 Revert "Move lower rectangle away a bit so rail fits"
    This reverts commit 67ef11ffba7b9d96acbaed33ddb451a6013469e5.
    [motor_mount_small.scad]
2016-07-30 Added File
    Added Long Tie Rails to the Old Extention. Mostly personal preference,
    like the old style for its modularity and plastic economy.
    [Old_extention_v2.stl]
2016-07-30 Updated 3d mesh
    Hopefully it will be printable now.
    [Old_extention_v2.stl]
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2016-08-03 Hole position tuning
    - updated middle gear hole position so assembly
    now fits inside the small case
    - stretched gear holes 2mm so there's some room
    for adjustment
    - note: need to print new rev gear two
    - preliminary support for different case sizes
    [bed_carriage.scad, bed_carriage.stl]
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2016-08-10 Add another 'layer' to bed carriage
    - this layer is to keep large gear bolts straight
    - meant to be installed on the oppsite side of the
    gears and attach to the large gear bolt
    [bed_carriage.scad, bed_carriage.stl]
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2016-08-28 Bed carriage update
    - add bolt holder sleeves
    - remove unneeded indents
    [bed_carriage.scad, bed_carriage.stl]
2016-08-28 Motor mount update
    - fix top tower hieght
    - make bolt holes so that motor position can be adjusted
    [motor_mount_small.scad, motor_mount_small.stl]
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2016-08-28 Change long bow tie scaling
    - were too loose
    [long_bow_tie.scad, long_bow_tie.stl]
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2016-08-30 Twist corner: use gears instead include
    - doesn't render gear model if uncommented in gears
    [twist_corner.scad]
2016-08-30 Tune bed carriage
    - add middle gear holes to motor part
    [bed_carriage.scad, bed_carriage.stl]
